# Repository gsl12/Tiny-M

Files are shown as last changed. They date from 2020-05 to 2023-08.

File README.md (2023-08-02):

# Tiny-M   
   
### !!!!!!!!!!!!!! August 2023 !!!!!!!!!!!!!!   
Due to a serious illness, I cannot continues the project.   
Unfortunately i cannot tell, when i could work again.   

[V5 beta](https://github.com/gsl12/Tiny-M-V5-beta)

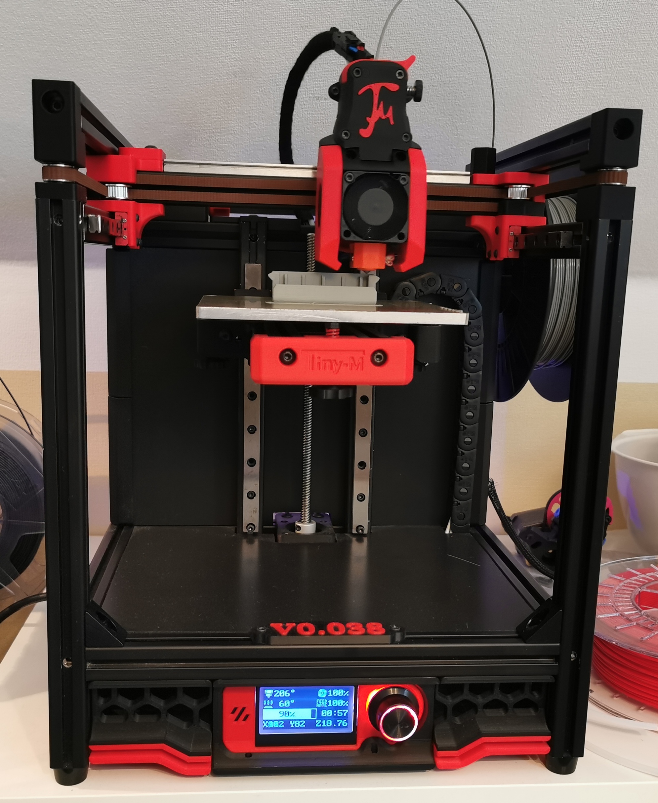
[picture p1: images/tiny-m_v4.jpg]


A compact printer with build volume: 150x150x150 mm

This is a Corona project.  
It is based on [Voron V0](https://github.com/VoronDesign/Voron-0) .  

Bowden and direct drive extruder using [CroXY's Sailfin](https://github.com/CroXY3D/Sailfin-Extruder), [Annex Engineering's Sherpa Mini](https://github.com/Annex-Engineering/Sherpa_Mini-Extruder) or [Bondtech's LGX Lite](https://www.bondtech.se/product/lgx-lite-extruder-custom/) are now available.  

### Current Version is V4:  

Latest source whole printer:  [Tiny-M V4 Onshape](https://cad.onshape.com/documents/f842588d372acab22a4ce687/w/3332acdd7c7bf7fc53ddefb6/e/ce1bfb58b96a9bb3b38b0502)

Old source is available at [Tiny-M V3 Onshape](https://cad.onshape.com/documents/d2a24a4147c3d522115f6ea5/w/d8f44be5c0a081fbf527e154/e/debb6c2779e27f86389232d5).

This is my first project of this kind. Maybe something will be missing, is not well documented, or just messy. I apologize for that.  Join the [Discord](https://discord.gg/tmZkjWs) to meet other Tiny-M builders and have your questions answered.

## Why the whole thing?

I had many 3D printer parts in my pocket from my old no longer used printer. 
I cleared out my pocket and took what I had in the box without buying anything new.
After checking all parts, I recognize, that I could build a converted Voron V0 with this parts.

### Hardware

    - 2020 Nut 5 I-Typ alu profiles (6mm wide slot Misumi 2020 will work).  Must have 4.0-4.2mm hole at ends.  B-Typ can work with Helicoils to give a 5mm tapped end.
    - Nema 17 stepper motors
    - 1x 200mm MGN12H for X
    - 2x 200mm MGN9H for Y
    - 2x 200mm MGN12H for Z
    - FYSETC Cheetah V1.1b (TMC2209) or SKR Mini E3 with TMC2209
    - 24V everywhere

### BOM
DRAFT BOM is available now. Thanks to CookieSN!  An updated BOM for V4 is currently in review.

WARNING ! The store Funssor on aliexpress sell a V0 kit with pictures of my Tiny-M. He use picture from github. To be clear IT IS NOT a Tiny-M Kit. Please don't buy it if you want to build a Tiny-M.

### Build Tips
There are 3 versions of the XY-Joins.  V4 is recommended.

- V2 - use 2GT 20T pulleys - No Set Screw Hub
    - The outer diameter of the flanges from the pulleys for XY Joins will not fit.
    - You will need to grind the flanges to fit.
- V3 - use 2GT 20T toothed idler and no M5 Nuts
- V4 - split into 3 parts
    - removed one M5 screw for better alignment
    - optimized belt path to use E3D idler (10mm high) or chinese (9mm high)
    - some design changes
    - more rigid

Parts are best printed out of ABS or ABS+ with 0.4 nozzle with 0.48 extrusion width, 0.2-0.3 layer height, 5 top/bottom layers, 4 perimeters, 40% infill (triangular recommended).  Skirts can be printed out of pretty much any filament type.

There are drill and tapping jigs if you wish to drill and tap your extrusions yourself.  The drilled holes are for blind joints and aren't necessary if using corner brackets.

[Mark Hoy's Excellent Build Log](https://github.com/mark-hoy/tiny-m-build)

[Aku's Build Pix](https://photos.google.com/share/AF1QipNcXcmM3RKy_vv-VFk4SFu25SVPCTLMsn6qd6mMj0eABvdKW5LyGL7gtdgspUF8wQ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)

### User Mods
There are several user mod STLs in the [usermods](https://github.com/gsl12/Tiny-M/tree/master/usermods) directory.

#### V4 Mods
[Belted Z Mod](https://github.com/gsl12/Tiny-M/tree/master/usermods/belted_z_mod)

[190^3 Mod which uses Prusa mini bed plates](https://github.com/gsl12/Tiny-M/tree/master/usermods/190mm_prusa_mini_mod)

[All Metal Bed Undercarriage](https://github.com/gsl12/Tiny-M/tree/master/usermods/all_metal_bed_undercarriage)

[5mm Shoulder Screw Mod, (also works with B-Typ extrusions)](https://github.com/gsl12/Tiny-M/tree/master/usermods/shoulder_screw_mod)

[5mm Dowel Pin Mod](https://github.com/gsl12/Tiny-M/tree/master/usermods/5mm_idler_pins)

[Rear Cable Guide](https://github.com/gsl12/Tiny-M/tree/master/usermods/rear_cable_guide)

[Tophat Mod](https://www.prusaprinters.org/prints/64115-tiny-m-voron0-mod-tophead) - Note, an official tophat is in development.

#### V3 Mods
[Xile's Sherpa Direct Drive Toolhead](https://github.com/Annex-Engineering/Sherpa_Mini-Extruder/tree/master/Toolheads/Xile_Tiny_M)

[Ocho Camino's Sailfin Direct Drive Toolhead](https://github.com/CroXY3D/Sailfin-Extruder)

### Discord

The [CroXY Discord](https://discord.gg/tmZkjWs) has a tiny-m channel where several Tiny-M builders hang out.  Be sure to check the #tiny-m-faq channel

# Images

V3  

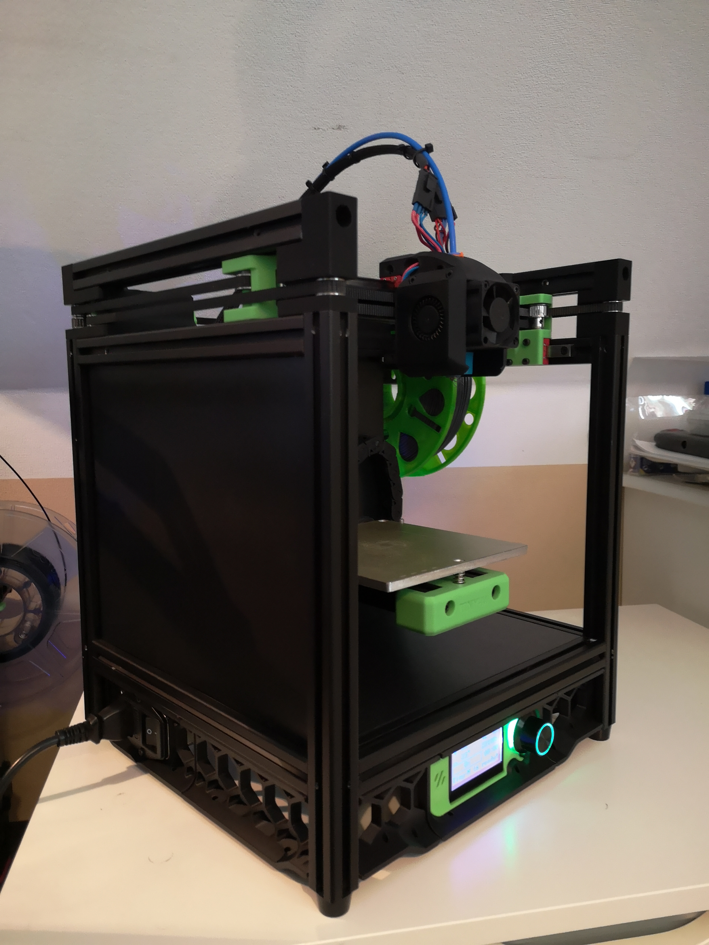
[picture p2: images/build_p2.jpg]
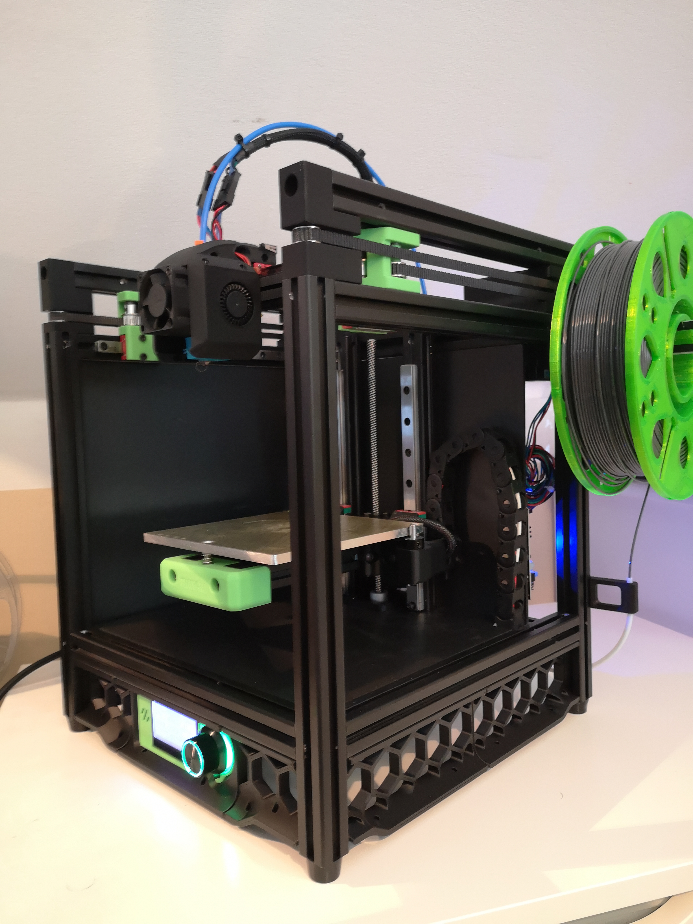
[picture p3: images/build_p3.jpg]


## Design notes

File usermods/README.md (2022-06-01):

### User mods

* tiny-m_tap_guide.stl : guide for tapping ends of 2020 extrusions (danielfmo)
* tiny-m_drill_guide.stl: drill guide for blind joint acccess holes (danielfmo)
* ab_drive_top_raised.STL : On some steppers the screws bottom out.  This thickens the plastic. (Xile)
* Knob_Wrench.stl : Tool to turn the tensioning knobs (Xile)
* Panel_Holder_1.STL : Panel holders keep panels from sagging - (Xile, modified from design by Anlin at Annex Engineering)
* PanelClip_v2_1.stl : Hold exterior panels on - (Xile, Modified from design by Anlin at Annnex Engineering)
* front_bed_mount_proud_text.stl : (Ocho Camino) Front of bed with text raised so you can do a filament swap.
* LRS-150_Mount.STL : Mount for Meanwell power supply (Xile)
* SKR_Mini_Mount.STL : Mount for SKR Mini (Xile)
* Raspi_Mount.STL : Mount for Raspberry Pi (Xile)
* Buck_Converter_Mount.STL : Mount for [Buck converter](https://smile.amazon.com/gp/product/B07N3QT628/ref=ppx_yo_dt_b_search_asin_title?ie=UTF8&psc=1]) for Raspberry Pi 5V (Xile) 
* Cover_No_Logo.STL : No logo version of screen cover
* door_handle: A handle for the enclosure door

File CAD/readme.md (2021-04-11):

# Current Version is V4:  

latest source whole printer:  [Tiny-M V4 Onshape](https://cad.onshape.com/documents/1523b676d2485ac19dbd60ec/w/d40ca3d72ed1f4079efb6497/e/a8deb399653e35f8f0a5baa5)

V4 folder includes separated CAD files for each V4 part.

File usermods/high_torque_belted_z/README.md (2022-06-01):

### High Torque Belted Z

- @AgentL3r#0333

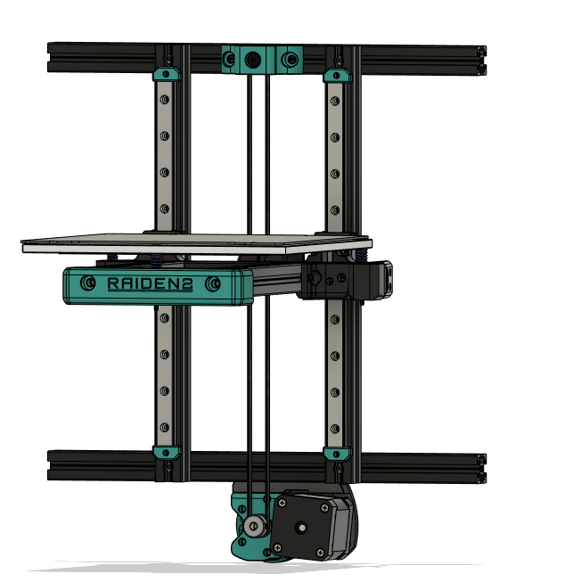
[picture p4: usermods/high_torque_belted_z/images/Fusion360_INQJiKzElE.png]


## Features and Rationale
- Allows for any size of NEMA17 motor to be used, increasing versatility and mitigates the need for slimline/pancake motors 
- Motors with higher detent torques can be used to prevent bed drop on power loss (after 4:1 gearing)
- Gearbox is mounted under the electronics enclosure leading to more space for electronics mounting
- Compatible with both 190mm³ and 150mm³ builds **MUST USE MODIFIED PARTS BY nehiLo#1732**
- Shoulder screw compatible upper z idler
- Arguably less Z artifacting due to no leadscrew
  
## Bill of Materials

Fasteners
- M3x5x4 mm threaded insert x5
- M3 washer (1mm) x3
- M3 shim (0.5mm) x3
- M3x6 BHCS x4
- M3x10 SHCS x4
- M3x20 SHCS x6
- M5 t-nut x7
- M5x10 BHCS x4
- M5x20 BHCS x2
- M5x28 BHCS OR M5x16 SHOULDER SCREW with 5mm shoulder x1
- M5x60 dowel pin

Motion
- F695-2RS bearing x2
- 20T 2GT pulley x2
- 80T 2GT pulley x1 (CAN ALSO USE PRINTED VORON M4 80T)
- 188mm 2GT 6mm belt loop
- some 2GT 6mm belt
- 20T 5mm bore idler

Electronics
- NEMA17 motor

## Assembly
It is best to refer to the CAD  model for guidance on how to build this system.

**Gearbox:**
Insert the four heatset inserts into the back of the shaft guide and press-fit the F695-2RS bearing as follows:
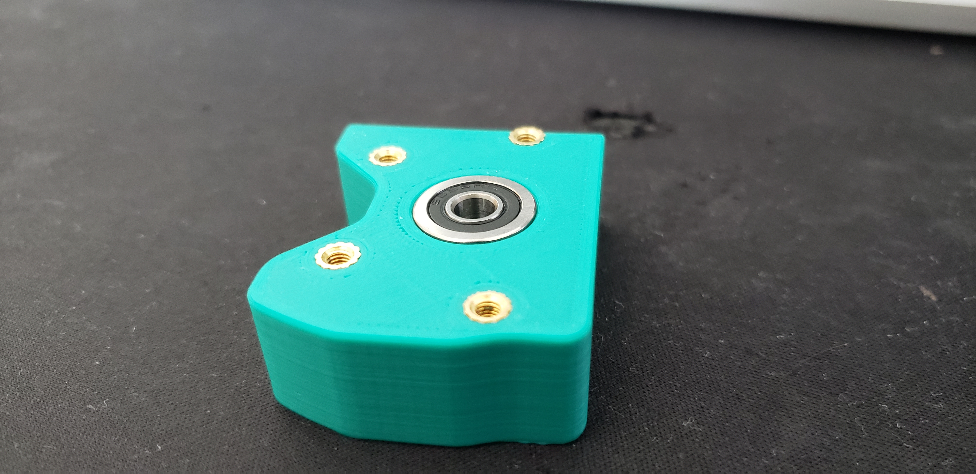
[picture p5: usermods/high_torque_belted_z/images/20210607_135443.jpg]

Press fit an F695-2RS bearing onto the motor plate.

Attach the motor plate to the bottom of the 2020 extrusion on your printer using two M5x10mm screws and two M5 t-nuts. Ensure you use the flat edge and a pair of calipers to correctly position the motor plate so that the pin is centered.

Attach the shaft guide using four M3x20 screws.

Insert the 5x60mm shaft through the motor plate and shaft guide, ensuring it spins freely in the bearings.

The pulleys can now be attached:

80T pulley --> printed spacer --> F695-2RS --> F695-2RS  --> 0.5mm shim --> 20T pulley

Tighten all grub screws.

Insert the remaining 20T pulley onto the shaft of the NEMA17 motor. Screw the motor to the motor plate using M3x10 screws (not fully tight as you'll need the motor to swivel for tension) and an M3 washer. During this, ensure the belt loop wraps around the 20T and 80T pulley. You can now tension the pulley and fully tighten all motor mounting screws. The gearbox is now complete.

**Idler:**
The upper idler is simple to assemble with a 20T idler sandwiched between two 0.5mm shims. Attach this to the top 2020 extrusion as per the CAD model.

**Tensioner:**
Insert the final heatset insert into the hole at the TOP of the tensioner.

Attach the tensioner to the back of the Z carriage using the M5x20mm screws and two M5 t-nuts. Positioning at this point isn't important.

Insert the two M3x20 screws into the tensioner. At this point, you can route the belt. 

The belt will wrap around the M3x20 screws so that the teeth indexes with itself, creating a very secure hold. Place the printed block in the center of the tensioner with the hole facing up.

Using the M3x6mm screws, secure the backplate.

Finally, use an M3x10 screw to tension the belt by pressing the printed block.

This assembly is fiddly and takes a while to get assembled - especially the belt tension. The system works very well and has given me excellent results.

Double check your spacing for everything prior to turning on the system - refer to the CAD if in doubt.

For any questions, feel free to get in touch with me on the TinyM Discord.

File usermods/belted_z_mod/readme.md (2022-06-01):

### Belted Z Mod for 150mm and 190mm Tiny-M

@quasi

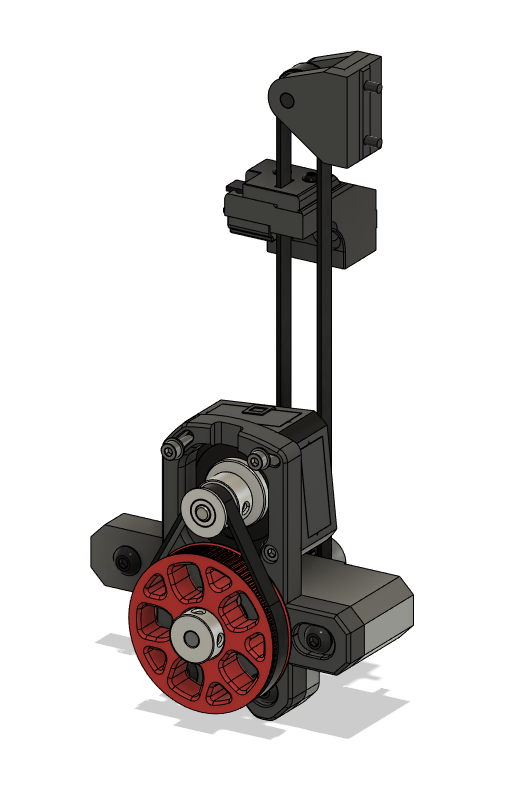
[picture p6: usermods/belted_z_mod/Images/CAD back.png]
Back


Modified from V0 belted z mod for Tiny-M printer, 2020 extrusions, and to upgrade some bolts from M3 to M5.

CAD shows a printed 80T gear because I copied that over from the V0 belted z files, but I used a metal 80T gear.

The M5x20mm screws need to be BHCS for clearance with 80T gear, but all other bolts can be either SHCS or BHCS.

Print the Bottom Frame Bracket 190.stl version if using this on a 190mm^3 Tiny-M

[sample printer.cfg changes](https://github.com/gsl12/Tiny-M/blob/master/usermods/belted_z_mod/beltedzstepper.cfg.txt)

#### BOM (US Sources)
##### Electronics	
- LDO NEMA17 42STH20-1004ASH	[PrintedSolid](https://www.printedsolid.com/collections/motors/products/ldo-nema-17-high-temp-voron-ldo-42sth20-1004ashvrn)  other 20 or a 25mm stepper 0.9 or 1.8 deg should work
##### Motion	
- F695-2RS Bearing [Amazon](https://www.amazon.com/F695-2RS-Bearing-5x13x4mm-Miniature-Bearings/dp/B07VMJLXLH)
- 1x 5mm shaft	78 mm	- I recommend measuring for yourself	[Amazon](https://www.amazon.com/Sydien-100mm-Solid-Stainless-Airplane/dp/B083LDBTLD)
- 1x 2GT Belt Loop (6mm wide) 188mm			[AliExpress](https://www.aliexpress.com/item/4000397043382.html)
- 1x 2GT Open Belt LL-2GT-6 (6mm wide) 10M			[AliExpress](https://www.aliexpress.com/item/32853559638.html)
- 1x 2GT 20T Pulley 6mm, 5mm Bore			[AliExpress](https://www.aliexpress.com/item/32995102911.html)
- 1x 2GT 16T Pulley 6mm, 5mm bore			[Amazon](https://www.amazon.com/gp/product/B01IMPM44O)
- 1x 2GT 80T Pulley 6mm, 5mm Bore			[AliExpress](https://www.aliexpress.com/item/32782605159.html)
- 1x 2GT 20T Toothed Idler 6mm, 5mm Bore		Alternate to 2 F695-2RS bearings	[AliExpress](https://www.aliexpress.com/item/32726309946.html) or better quality: [AliExpress](https://www.aliexpress.com/item/33023133633.html)
#### Hardware	
- Xx 5x10x0.5 Shim Ring			[AliExpress](https://www.aliexpress.com/item/32917948919.html) Qty as necessary.  
- 1x M3x5x4 Heatset Inserts		[AliExpress](https://www.aliexpress.com/item/4000232858343.html?spm=a2g0s.9042311.0.0.21164c4dGhWHhY)
- 2x M3 roll in T-nuts		[AliExpress](https://www.aliexpress.com/item/32805163712.html)
- 4x M5 roll in T-nuts			[AliExpress](https://www.aliexpress.com/item/32805163712.html)
- 2x M3 washer			
- 1x M5x40 SHCS			
- 3x M5x20 BHCS		These NEED to be BHCS for clearance with the 80T gear, all others can be SHCS or BHCS interchangeably	
- 1x M5x16 BHCS			
- 3x M3x12 SHCS			
- 1x M3x20 SHCS

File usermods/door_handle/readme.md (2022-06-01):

The original model provided no handle for the door, so i made one. It is derivatived from the Voron 0.1 door handle. I also added fitting corner pieces.

BOM:
- 2\* M3\*10 screws
- 2\* M3 t-nuts or hammer nuts
- VHB tape
- 8\* 6 mm x 3 mm magnets  

DSCF0841

DSCF0839

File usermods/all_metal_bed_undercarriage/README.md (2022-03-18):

### All Metal Bed Undercarriage

- @Ocho Camino

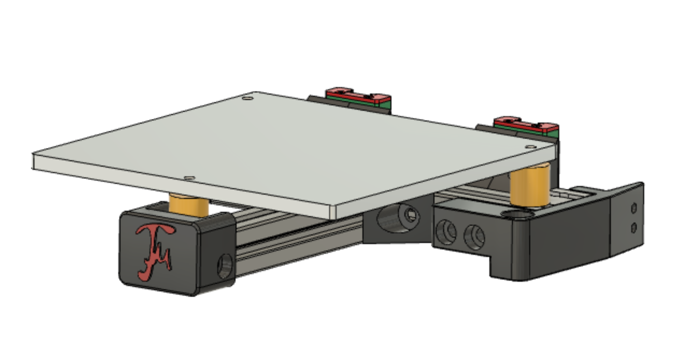
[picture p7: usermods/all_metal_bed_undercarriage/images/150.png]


## Rationale
The existing bed mounts are made of ABS and flex somewhat.   Making the entire bed undercarriage out of metal greatly reduces this flex.

## Status

  Alpha.  Still testing.  There could be some changes.
  
## BOM

150mm Bed:
- 1x HFSB5-2020-160-AH80-AV10-BV150
- 1x HFSB5-2020-160 (with 4 3mm clearance holes drilled for the MGN12 mount screws. Use MGN12_drill_jig.stl)
- 1x HFSB5-2020-133-RTP-AV10 (Misumi). 

190mm Bed:
- 1x HFSB5-2020-200-AH100-AV10-BV190 
- 1x HSFB5-2020-200 (with 4 3mm clearance holes drilled for the MGN12 mount screws.  Use MGN12_drill_jig.stl)
- 1x HFSB5-2020-173-RTP-AV10

Common:
- 6x Openbuilds Angle Brackets [Openbuilds](https://openbuildspartstore.com/black-angle-corner-connector/) [Ali Express](https://www.aliexpress.com/item/32899575950.html)
- 3x 16mm long silicone bed mounts [Amazon](https://smile.amazon.com/dp/B07RZKF8MB?psc=1&ref=ppx_yo2_dt_b_product_details)
- 3x Bed Adjusters (reuse existing) [Ali Experss Style B or D](https://www.aliexpress.com/item/4000421280308.html)
- 3x 45mm (or 50mm) FHCS screws.  45s protrude only 2.3 mm below the extrusion, so 50 is probably better.
- 4x M3 washers (at least 6mm OD) - [ALT Ali Bling](https://www.aliexpress.com/item/32968161596.html)
- 4x M3x8 SHCS (might need M3x10 with the Alt Ali Bling)
- 11x M5x6 BHCS
- 1x M5x12 SHCS
- 1x M5x16 SHCS

## Assembly

Print the parts (ok, it's not all metal, but the load bearing parts are). The nosepiece can be printed with a filament swap for a contrasting color for the logo.  

Note the rear two holes on the bed are in slightly different positions than on stock Tiny-M.  They are 12mm from the rear.
Use the template (TBD) to drill the two countersunk M3 holes.   

The underbed assembly is made of 3 pieces of 2020.  The rear piece attaches to the MGN12 cars.  The middle piece sisters to the rear piece and also supports the bed at each end in the rear.  The front piece is the forward pointing spar that supports the bed at the middle in the front.

The rear 2020 piece will need to be drilled with 4 3mm clearance holes to attach it to the MGN12 car.  Use the MGN12_drill_jig.stl to drill these holes, from each side of the 2020.

If you ordered the other 2020 parts without Misumi drilling for you, you will need to use the drill guide. The middle 2020 that is is sistered to the rear 2020 piece needs a 3mm vertical clearance hole 10mm from each end, and a 5mm horizontal clearance hole 30mm from each end (middle_front_drill_jig.stl).   Additionally that piece needs a 5mm horiztonal clearance hole centered on the extrusion - use middle_jig.stl centered on the extrusion.

The front piece is tapped M5 at the rear and has a 3mm clearance hole drilled vertically 10mm from the front of it (middle_front_drill_jig.stl).

Assemble the middle and front spar 2020 pieces to form a tee.   The two angle brackets that support the forward spar can be any type of angle bracket. Make sure this connection is solid and doesn't twist or flex.   Attach the spar to the tapped hole with a M3x8 BHCS for more rigidity. 

The Openbuilds corner brackts screw into the top screw holes of the MGN12H cars. Attach them to the rear 2020 piece.  The rear 2020 is attached to the lower screw holes of the MGN12H car via M3x16 SHCS.

Attach the tee piece to the rear piece with 2 M5x6 BHCS

The rest of the parts assembly should be straightforward.

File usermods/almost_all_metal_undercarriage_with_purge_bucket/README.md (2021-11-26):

# Almost All Metal Bed Undercarriage with Purge Bucket

- @DanielO

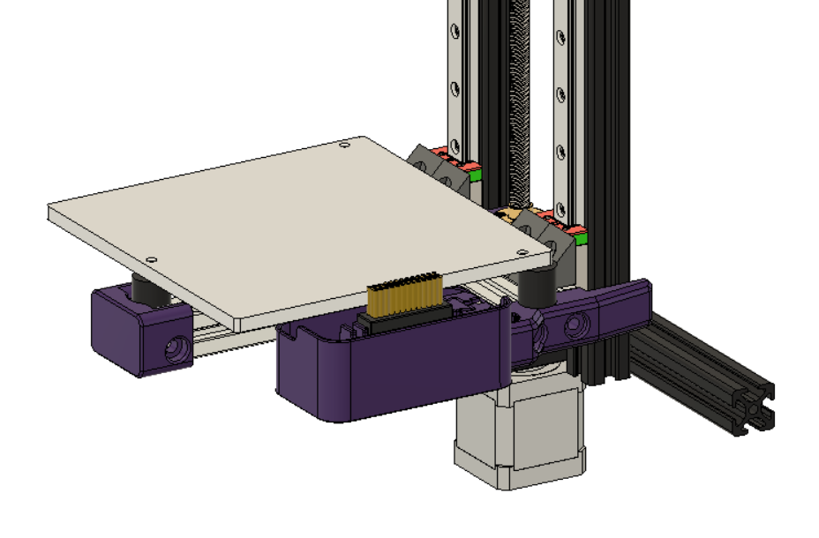
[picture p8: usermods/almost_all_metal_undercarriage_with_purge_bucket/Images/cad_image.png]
CAD

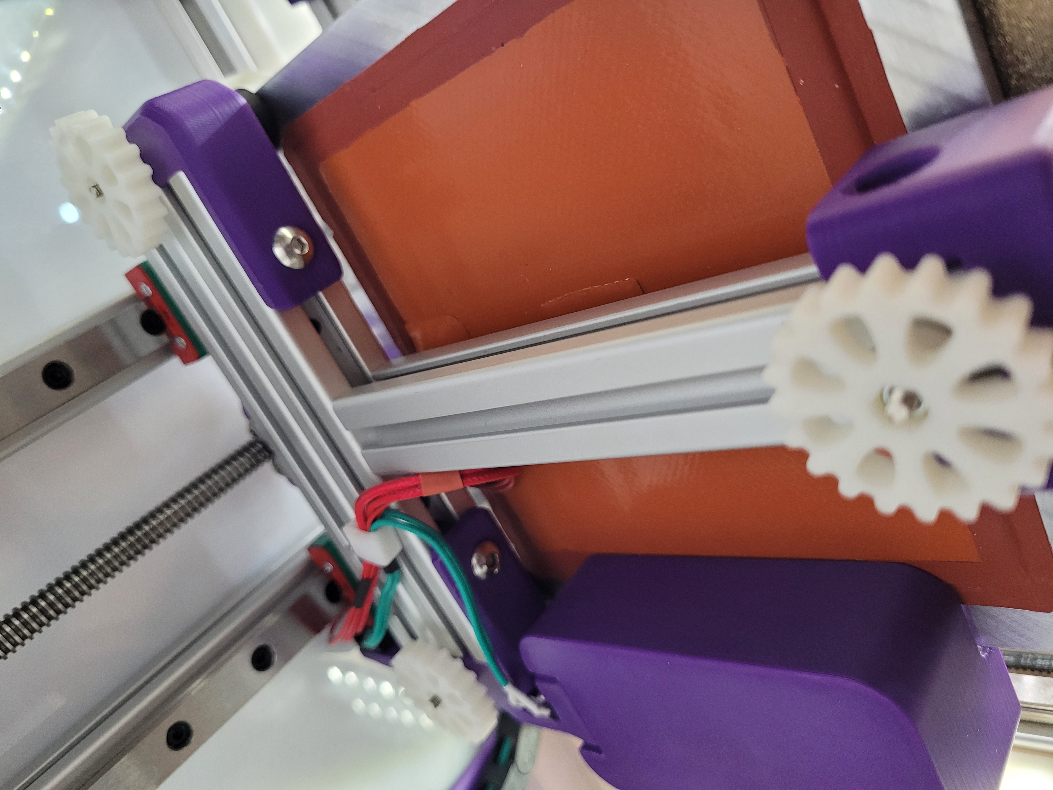
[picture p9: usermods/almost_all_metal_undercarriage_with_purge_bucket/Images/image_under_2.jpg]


## Rationale

The goal was to to create a all meter undercarriage mount inspired in the one created by @Ocho Camino, but using the default BOM extrusions e.g. 3x 130mm long for the 150mm2 version.

The purge bucket and brush were inspired in the [Annex purge bucket](https://github.com/Annex-Engineering/Other_Printer_Mods/tree/master/All_Printers/Purge_Brush_Bucket).

## Status

Tested and validated in a 150mm bed, though in retrospective some improvements could be made:

- move the z endstop a few milimets up in order to be able to use the default BOM 33mm long shaft.
- dimention the purge bucket for the 150mm bed, the available one might be too long.
- design a mount for a belted z mod

## Print Parts

Just need to print one of each STL/3mf.
And the [brush_holder_x1_rev1.STL](https://github.com/Annex-Engineering/Other_Printer_Mods/blob/master/All_Printers/Purge_Brush_Bucket/STLs/brush_holder_x1_rev1.STL) from Annex github.

## BOM

### 150mm Bed

- 3x 130mm long extrusions, from BOM
- 4x M5x8mm for the lead screw mount
- 2x M5x8mm for the from bed mount
- 4x M5x16mm for the side bed mounts
- 3x M5x30mm for holding the extrusions together
- 4x M3x18mm for holding the extrusions against the carts
- 4x M3x10mm and washers for holding the 90deg corners against the carts
- 4x M5x8mm for holding the 90deg corners against extrusions
- a few other M3x8mm for holding the cable chain and the brush
- 4x 6x3mm magnets for the bucket

### 190mm Bed

- not tested / adapted (but should be the same hardware and STLs as the 150mm)

## Klipper Macros for brush and bucket

Node: could and should be improved using variables

```clojure
[gcode_macro NOZZLE_CLEAN]
gcode:
    SAVE_GCODE_STATE NAME=nozzle_clean_state
    G1 X152 Y58 F3000
    G1 Z0.6     F3000
    ; Purge filament macro
    PURGE_FILAMENT
    G90
    ; clean twice
    G1 X152 Y58 F6000
    G1 Y105
    G1 Y58
    G1 Y105
    G1 Y58
    ; Retract
    ;G10
    ; clean once
    G1 Y105
    G1 Y58
    RESTORE_GCODE_STATE NAME=nozzle_clean_state
```

In START_PRINT macro do something like

```clojure
[gcode_macro START_PRINT]
gcode:
  ;================ SET VARIABLES ====================
  {% set T_BED = params.T_BED|default(60)|float %}
  {% set T_EXTRUDER = params.T_EXTRUDER|default(205)|float %}
  TURN_OFF_HEATERS
  M106 S0
  G21                           ; [mm] mode
  G90                           ; Absolute position mode
  M220 S100                     ; reset speed multiplier
  G92 E0                        ; reset e count
  M83                           ; relative Extruder mode
  ;================ INITIALISATION ====================
  G28                           ;  first homing
  ;================ WARM UP ===========================
  G1 X152 Y58 Z5 F3000          ; move nozzle to brush
  {% if printer.heater_bed.temperature < params.T_BED|float*0.85 %}
      M190 S{params.T_BED|float*0.85}
  {% endif %}
  M140 S{T_BED}
  ;G1 X152 Y105 Z0.4 F3000      ; move to approx starting location
  M104 S{T_EXTRUDER|int - 30}   ; set no-ooze extruder temp
  M109 S{T_EXTRUDER|int - 30}   ; wait no-ooze for extruder temp
  ;----------------------- CLEANING---------------------------------
  NOZZLE_CLEAN                  ; call the macro that will clean the nozzle
  ;----------------------- PRECISE HOME-----------------------------
  G28 Z                         ; home z again with nozzle hot
  G1 X152 Y58 Z0.2 F3000        ; move to approx starting location
  ;----------------------- FINAL TEMPS -----------------------------
  M140 S{T_BED}                 ; set final bed temp
  M190 S{T_BED}                 ; wait for final bed temp
  M104 S{T_EXTRUDER}            ; set final extruder temp
  M109 S{T_EXTRUDER}            ; wait for final extruder temp
  ;-----------------------PRIMING-----------------------------------
  PRIME_LINE
  G10;
  G1 Y58                        ; rub on the brush one more time
  G1 Y105
  G1 Y58                        ; move to approx starting location
  G92 E0;                       ; set extruder to Zero
  G1 E0 F100
```

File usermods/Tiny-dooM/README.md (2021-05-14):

### Tiny-dooM

- @Ocho Camino

An outer enclosure around the Tiny-M printer.  This has only been designed in CAD.  Nothing has been done IRL.

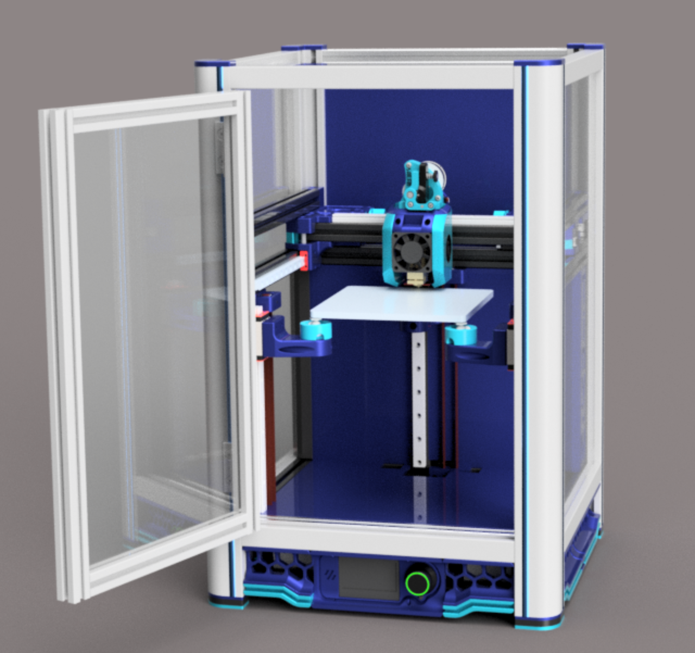
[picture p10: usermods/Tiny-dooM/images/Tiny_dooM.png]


#### BOM

Nothing is changed from the default Tiny-M BOM.  However you will need to drill 2 blind joint access holes in the 4 z corner extrusions.  Those holes should be approx 30mm from the ends and face fore and aft.  They are used to attach the Tiny-M to the dooM frame.

For a 190^3 Tiny-dooM add 50mm to every extrusion length

- 4x HFSR5-404020-500 Corner Posts
- Non-smooth faced extrusion option
  - 8x HFS5-2020-260 Top and bottom horizontals
  - 2x HFS5-2020-217 Front door horizontals
  - 2x HFS5-2020-408 Front door verticals
- Smooth faced extrusion option
  - 2x HFS5-2020-260 Top and bottom rear horizontals (Slots exposed for mounting things)
  - 3x HFSF5-2020-260 - Bottom front, left and right horizontals
  - 3x HFST5-2020-260 - Top front, left and right horizontals
  - 2x HFSF5-2020-217 Front door horizontals
  - 2x HFSF5-2020-408 Front door verticals - you will need to drill holes for hinges and handle
- 2x Hinges [Zyltech](https://www.zyltech.com/aluminum-swing-door-hinge-for-20mm-extrusion-w-mounting-hardware/) alt: HHPNL5-SST hinges
- 24x Internal Corner Brackets [Zyltech](https://www.zyltech.com/t-slot-l-type-90-degree-2020-inside-bracket-12-pack/)
- Door Catch TBD
- Optional: Ninjaflex or similar TPU for feet

Total Hardware Cost for 150 Tiny-dooM (no panels): ~$85

#### Printed Parts

- 4x Top trim pieces
- 4x Feet.  Optionally print black portion using Ninjaflex or similar TPU by filament swap.  Use XX% infill
- TBD Panel retention:  Double pane?  In slot or slight inset from frame?

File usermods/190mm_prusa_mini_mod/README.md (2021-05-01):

### 190^3 Build volume which can use the Prusa Mini Bed Plate.

- @Ocho Camino & @AgentL3r
- Skirts by @AgentL3r

The changes for a 190^3 build volume are fairly simple.   
- All frame extrusions need to be 50mm longer
   * 11x 2020 310mm  (note one more than normal Tiny-M.  This is used as a cross brace about halfway up in the front to stiffen the frame)
   * 4x	2020 350mm
   * 2x	2020 300mm
- All bed extrusions need to be 40 mm longer
   * 3x	2020 170mm
- 1X 250mm MGN12H for X (RobotDigg SUS 440C highly recommended) 
- 2x 250mm MGN9H for Y 
- 2X 250mm MGN12H for Z
- 250mm TR8x4 leadscrew
- Mic6 bed should be 190x190x6mm.  Template for drilling are in the STLs subdir here.
- Bed heater should be 150x150mm.   [Keenovo or AliExpress](https://www.aliexpress.com/item/4000271859036.html?spm=a2g0s.9042311.0.0.27424c4dSLLDSs)
- Three parts need to be 40mm wider.  The front nosepiece and the upper and lower Z supports.  They are in the STLs subdir here
- Skirts are changed.  STLs and CAD by @AgentL3r are here

Note that the nosepiece is modded with proud text, so you can print it text up and do a filament swap for contrasting text.  The holes in the nosepiece have a membrane for printability that must be drilled out 5mm.

If you wish to use blind holes, the extrusion BOM:
- 2x HFSB5-2020-170-TPW		Z carriage.
- 1x HFSB5-2020-170-AH40-BH130	 Z carriage. 
- 2x HFSB5-2020-300-LCV-RCV		Vertical extrusions.
- 1x HFSB5-2020-310	X axis extrusion. 
- 3x HFSB5-2020-310-TPW	Lower front and upper left/right extrusions. 
- 4x HFSB5-2020-310-TPW-AH274		Left and right extrusions. 
- 2x HFSB5-2020-310-TPW-AH93.5-BH216.5	Horizontal Z extrusions.
- 2x HFSB5-2020-350-TPW-RCH-AP60		Front vertical extrusions. 
- 2x HFSB5-2020-350-TPW-RCH-AH60		Rear vertical extrusions.

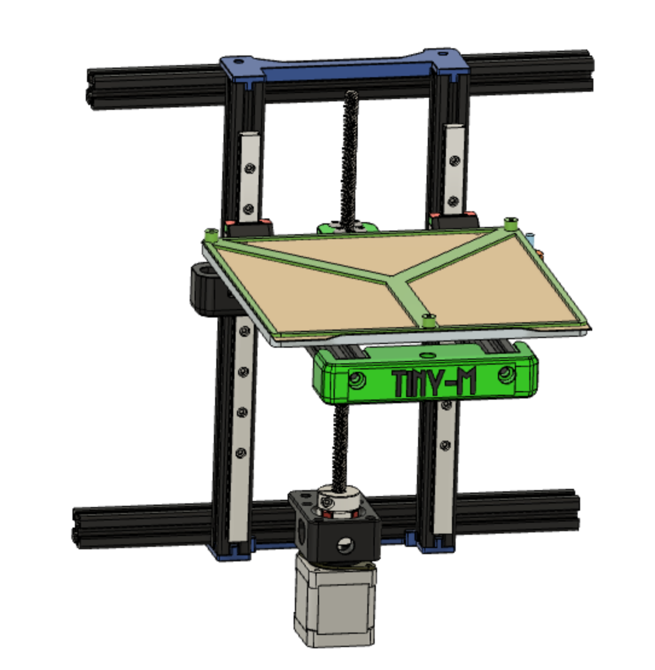
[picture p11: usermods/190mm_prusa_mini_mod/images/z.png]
190^3 Z Assembly


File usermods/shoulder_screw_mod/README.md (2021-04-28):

### Shoulder Screw Mod

by Ocho Camino

This is a mod to use shoulder screws instead of regular metric screws as the shafts for the idlers to ride upon.  

#### Rationale

Shoulder screws are machined to specified dimensions vs screws which are undersized and often have a rough surface.  With undersized screws the contact area of the screw to the inner race of the bearing is much less (ideally a line), creating excessive Hertzian contact stress.  This is hard on the bearing and can create imprecision in the motion of the machine.

#### Description

This mod either uses Misumi 5mm shoulder screws which have M3 threads on the end, or McMaster or other shoulder screws which have M4 threads.  The thread lengths are important on the McMaster M4 version, so if substituting other sources you may need to remove some thread if it's too long and bottoms out.

On the four corners of Tiny-M the ends of the 2020s are tapped M5 for M5 screws.  If using Misumi shoulders, you will need thread adapters.   If using M4 shoulders you will need M4 Helicoils

Print the replacement parts in the STL directory here.

Total cost of this mod is about $25-$30.

#### MISUMI M3 THREADED SHOULDERS
  * 6x 5mmx30 Shoulder Screws M3 Threads, Misumi [SMSB5-30](https://us.misumi-ec.com/vona2/detail/110300249140/?ProductCode=SMSB5-30)
  * 4x 5mmx20 Shoulder Screws M3 Threads, Misumi [SMSB5-20](https://us.misumi-ec.com/vona2/detail/110300249140/?ProductCode=SMSB5-20)
  * 4x M3-M5 308 Type Thread Adapters, AliExpress [M3-M5 308](https://www.aliexpress.com/item/32817733610.html)
  * 2x M3 Tee Nuts

Print the replacement parts, except the M4 versions in the STL directory here.  Install the thread adapters on the 4 M5x30 shoulder screws and secure with Loc-Tite.   These may then be threaded into the tapped M5 hole on the end of the 2020 vertical corner extrusions.  The Tee nuts accept the shoulder screw for the front idler on the AB drives
 
#### FILASTRUDER OR MCMASTER M4 THREADED SHOULDERS
  * 4x 5mmx30 Shoulder Screws, 5-9mm long M4 threads for corners, [Filastruder](https://www.filastruder.com/products/shoulder-screws-bolts?_pos=1&_sid=c5a60b2bd&_ss=r&variant=32520243380295) or [McMaster 92981A055](https://www.mcmaster.com/92981A055/)
  * 2x 5mmx30 Shoulder Screws 5mm long M4 threads for AB drives, [Filastruder](https://www.filastruder.com/products/shoulder-screws-bolts?_pos=1&_sid=c5a60b2bd&_ss=r&variant=32520243380295) or [McMaster 90278A376](https://www.mcmaster.com/90278A376/)
  * 4x 5mmx20 Shoulder Screws, 5-9mm long M4 threads for XY Joins, [Filastruder](https://www.filastruder.com/products/shoulder-screws-bolts?_pos=1&_sid=c5a60b2bd&_ss=r&variant=16712533868615) or [McMaster 92981A042](https://www.mcmaster.com/92981A042/)
  * 1x M4 Helicoil kit, AliExpress [M4x0.7](https://www.aliexpress.com/item/4001157165014.html) or [McMaster 91732A946](https://www.mcmaster.com/91732A946/)
  * 2x M4 Tee Nuts

Print the replacement parts (the M4 versions) in the STL directory here.  Install M4 helicoils in the 4 corner 2020 extrusions.   The Tee nuts accept the shoulder screw for the front idler on the AB drives 

#### EU Folks using 20x20 B-type groove 6 and M4 THREADED SHOULDERS
  * 4x 5mmx30 Shoulder Screws, 8mm long M4 threads for corners, Drasse [460119196](https://www.drabbe.nl/p/iso-7379-5-m4-30/100351/)
  * 2x 5mmx25 Shoulder Screws 8mm long M4 threads for AB drives, Drasse [460119221](https://www.drabbe.nl/p/iso-7379-5-m4-25/100350/)
  * 4x 5mmx20 Shoulder Screws, 8mm long M4 threads for XY Joins Drasse [460119215](https://www.drabbe.nl/p/iso-7379-5-m4-20/100349/)
  * 4x M4-M6 308 Type Thread Adapters, AliExpress [M4-M6 308](https://www.aliexpress.com/item/32817733610.html)
  * 2x M4 Tee Nuts

Print the replacement parts, except the M4 versions in the STL directory here.  Install the thread adapters on the 4 M5x30 shoulder screws and secure with Loc-Tite.   These may then be threaded into the tapped M6 hole on the end of the 2020 B-type groove 6 vertical corner extrusions. The Tee nuts accept the shoulder screw for the front idler on the AB drives

Note, the 5mm shoulders with M4 threads can be sourced from China.  [one possible source - not verified](https://www.aliexpress.com/item/1005001698010943)

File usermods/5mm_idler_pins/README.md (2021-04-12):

### 5mm Dowel Pin Mod
- Ocho Camino

NOTE:  The 5mm shoulder screw mod is recommended over this mod.

This is a mod to use 5mm dowel pins instead of fasteners for the idlers to ride on.  It is based on the V4 gantry.

#### RATIONALE
Dowel pins are exactly 5mm in diameter vs the typical 4.8mm of M5 screws.  This provides a better bearing surface for the inner race of the idler bearings.  Bearing on threads is especially problematic.
It should prolong the life of the bearings and improve print quality because there's signicantly less play.

This mod has not been tested yet!  I am slightly concerned about the rigidity of the front idler mounts as they aren't connected to the corner posts anymore.   

#### BOM
  - 10x 5mmx32mm dowel pins.  [McMaster](https://www.mcmaster.com/91585A569/).  30mm pins may be substituted.  You may also cut down 5mm drill rod or other precision stock to length.  Note some holes can accomodate longer than 32mm pins, so measure and make them longer if need be.

#### INSTALLATION OF PINS
You will probably need to drill out the holes in the parts with a 5mm drill bit.  The idler bearings and toothed idler should slide along the length of the pin.  If the pin is oversized (most dowel pins are), chuck it up in a drill and use 400 grit sandpaper to reduce the diameter.  You shouldn't need to remove more than 0.01mm so check as you go.   

Press the pins into the parts while capturing the bearings/washers/idlers.  If you overcompress the part and bind the bearings, you may need to gently pry the assembly apart a tiny bit.  If the pin is loose, place some thin CA adhesive in the pin holes top and bottom.

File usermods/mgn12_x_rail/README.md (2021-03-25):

Mods to use a MGN12 instead of a MGN9 rail for X.  By FL62michi

NOTE, V4 gantry uses MGN12 rail.

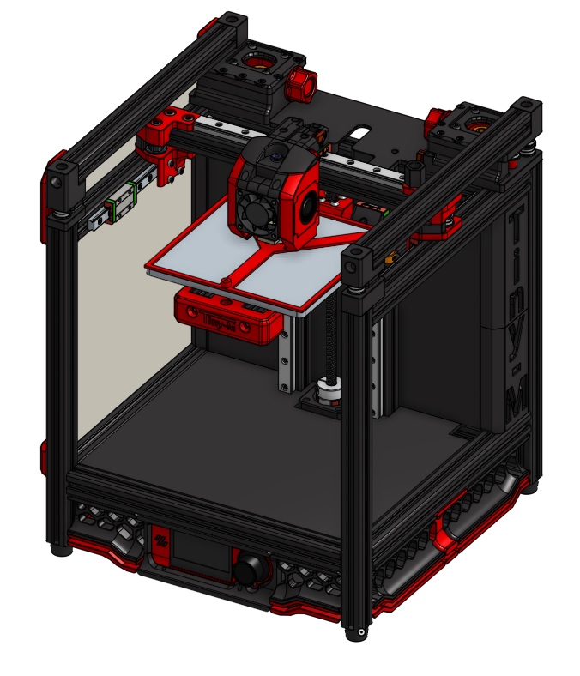
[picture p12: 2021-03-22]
images/CAD_V4.jpg

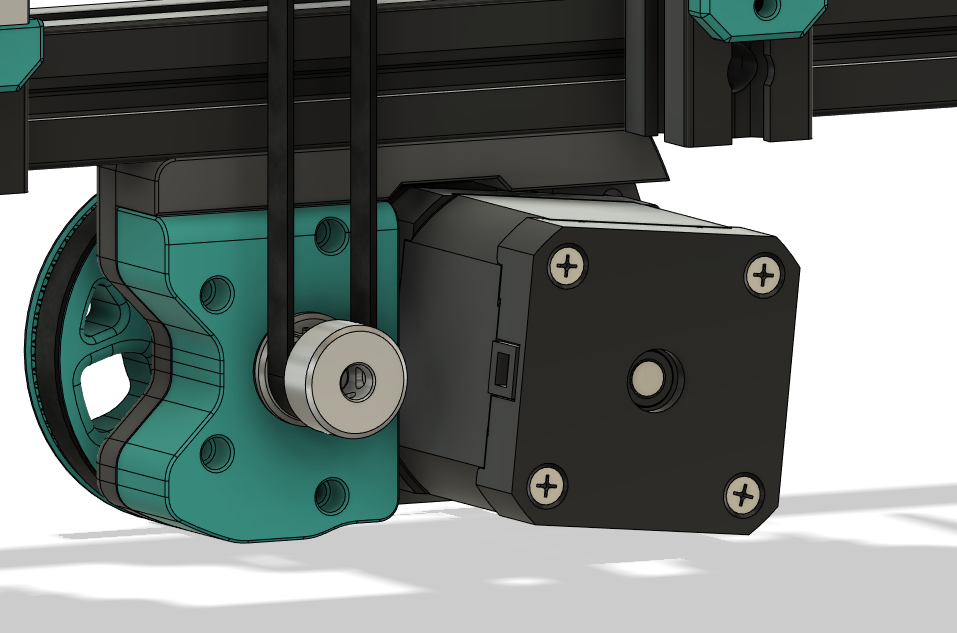
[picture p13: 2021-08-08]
usermods/high_torque_belted_z/images/Fusion360_5fomUjJK1f.png

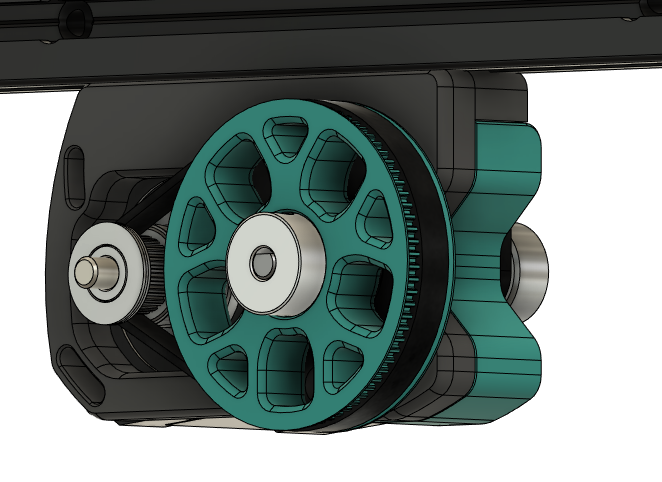
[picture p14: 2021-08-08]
usermods/high_torque_belted_z/images/Fusion360_azjq1ihh6n.png

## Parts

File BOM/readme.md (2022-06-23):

The .XLSX bom here is ancient and deprecated.

[Recommended V4 BOM with US, China and some EU sources](https://docs.google.com/spreadsheets/d/e/2PACX-1vQKTQRPsufotex2pgKZs6gdDjUGlbPzPMrz_vgNp8odzEya9Jntykz1X8XHGsFwYE4CXp_6QBfreYBq/pubhtml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)

[Preliminary (V3?) Google Sheets Version with US Sources](https://docs.google.com/spreadsheets/d/1UV62ADl2gtK5vL0fV1nwevR6O9Ppzs0MBe7jnsI-jo4/edit#gid=1444976440)

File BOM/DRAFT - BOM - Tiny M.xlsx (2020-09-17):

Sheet: BOM_Tiny_M
Category | Component | Standard | Qty | Sourcing DE | AliExpress Source | Alternative Source | Notes
Hardware | 5x10x0.5 Shim Ring | DIN 988 5x10x0.5 Shim Ring | 17
Hardware | 5x10x1 Shim Ring | DIN 988 5x10x1 Shim Ring | 6
Hardware | 5x30mm | shaft 5x30mm | 1
Hardware | M2.5x12 SHCS (for dragon hotend only) | DIN 912 M2.5x12 | 4
Hardware | M2x10 self tapping screw for Plastic |  | 15
Hardware | M3 - T-Nut | M3 - T-Nut | 6
Hardware | M3 Brass Heatstake Inserts | M3x5.0x4.0 | 15
Hardware | M3 Nut | DIN 934 M3 Nut | 14
Hardware | M3x10 SHCS | DIN 912 M3x10 | 2
Hardware | M3x12 SHCS | DIN 912 M3x12 | 2
Hardware | M3x20 SHCS | DIN 912 M3x20 | 2
Hardware | M3x25 SHCS | DIN 912 M3x25 | 2
Hardware | M3x30 SHCS | DIN 912 M3x30 | 8
Hardware | M3x35 SHCS | DIN 912 M3x35 | 8
Hardware | M3x40 SHCS | DIN 912 M3x40 | 12
Hardware | M3x50 SHCS | DIN 912 M3x50 | 4
Hardware | M3x8 SHCS | DIN 912 M3x8 | 99
Hardware | M4x8 SHCS | DIN 912 M4x8 | 4
Hardware | M5 T-Nut | M5 T-Nut | 18
Hardware | M5x10 BHCS | ISO 7380-1 M5x10 | 19
Hardware | M5x15 BHCS | ISO 7380-1 M5x15 | 1
Hardware | M5x16 BHCS | ISO 7380-1 M5x16 | 4
Hardware | M5x20 BHCS | ISO 7380-1 M5x20 | 1
Hardware | M5x30 BHCS | ISO 7380-1 M5x30 | 4
Hardware | M5x35 BHCS | ISO 7380-1 M5x35 | 4
Hardware | M5x40 SHCS | DIN 912 M5x40 | 4
Frame | Frame 2020 Typ I 5mm | 300mm | 4 | MyAluProfil.de (https://www.myaluprofil.de/aluminiumprofil-20x20-nut-5-i-typ-.html)
Frame | Frame 2020 Typ I 5mm | 260mm | 10 | MyAluProfil.de (https://www.myaluprofil.de/aluminiumprofil-20x20-nut-5-i-typ-.html)
Frame | Frame 2020 Typ I 5mm | 250mm | 2 | MyAluProfil.de
Frame | Frame 2020 Typ I 5mm | 130mm | 3 | MyAluProfil.de
Electronic | Nema 17 Motor 17HS19-2004S | 17HS19-2004S | 3
Electronic | Omron Mouse Button - Micro Switch | D2F-5L | 4
Electronic | TL dragon hotend |  | 1
Electronic | V6 Hotend 24V | V6 Hotend | 1
Electronic | 4010 Blower Fan | 40x40x10 Blower Fan v1 | 4
Electronic | 4020 DC Fan 24V | 40x40x20 DC Fan | 2
Electronic | Mean Well LRS-150-24 | LRS-150-24 | 1 |  |  |  | Needed for the main electronis (board, motors, lcd, etc.)
Electronic | Mean Well LRS-350-24V | LRS-350-24V | 1 |  |  |  | Needed if you use a 24V heated bed. If not you must use a 110V/220V heated bed.
Electronic | Raspberry Pi 4 | 2GB or 4GB Version | 1 |  |  |  | If you have a Pi 3 you can use this also
Electronic | DC-DC 5V 3A converter |  | 1
Electronic | SKR E3 Mini | Bigtreetech SKR E3 Mini | 1
Electronic | Fysetc Mini 12864 | LCD Display | 1
Motion | GT2 20T Pulley 6mm, 5mm Bore | Powdge GT2 20T Pulley 6mm, 5mm Bore | 3
Motion | F695-2RS | F695-2RS bearing | 20
Motion | 2GT-20T-idler | 2GT-20T-idler | 2
Motion | MGN9-200mm | MGN9 200mm | 3
Motion | MGN12_200mm | linear rail MGN12 200mm | 2
Motion | TR8x8 Lead Screw Nut | lead screw TR8x8 215mm | 1
Motion | 5x8 flexible spider coupler | Stepper Coupler D25L30 | 1
Motion | Nema 17 Damper |  | 1
Buildplate | MIC6 6mm Plate - 150x150mm |  | 1
Buildplate | Silicone AC 120V/240V Heater 100x100mm 100W |  | 1
Buildplate | PEI + 3M 468P (200MP) |  | 1
Buildplate | yellow die springs 8x4x20mm |  | 3
Buildplate | Spring Steel Flex Buildplate 150x150mm (OPTIONAL)
Extruder | Nema 17 Motor 17HS19-2004S | 17HS08-1004S | 1
Extruder | BMG Kit |  | 1
Extruder | PFTE Tube 1m |  | 2
Mics. | Rubber Feed - 21x12 |  | 4 | Amazon.de (https://www.amazon.de/gp/product/B008LTY1NO/ref=ppx_yo_dt_b_asin_title_o00_s00?ie=UTF8&psc=1)
Mics. | Panels side |  | 2
Mics. | Panel bottom |  | 1
Mics. | panel back |  | 1

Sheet: Screw_Consolidated
Hardware | 5x10x0.5 Shim Ring | DIN 988 5x10x0.5 Shim Ring | 6 | x | Hardware | 5x10x0.5 Shim Ring | DIN 988 5x10x0.5 Shim Ring | 17
hardware | 5x10x0.5 Shim Ring | DIN 988 5x10x0.5 Shim Ring | 11 | x | Hardware | 5x10x1 Shim Ring | DIN 988 5x10x1 Shim Ring | 6
Hardware | 5x10x1 Shim Ring | DIN 988 5x10x1 Shim Ring | 1 | x | Hardware | 5x30mm | shaft 5x30mm | 1
Hardware | 5x10x1 Shim Ring | DIN 988 5x10x1 Shim Ring | 5 | x | Hardware | M2.5x12 SHCS (for dragon hotend only) | DIN 912 M2.5x12 | 4
Hardware | 5x30mm | shaft 5x30mm | 1 | x | Hardware | M2x10 self tapping screw for Plastic |  | 15
Hardware | DIN 912 M3x8 | DIN 912 M3x8 | 16 | x | Hardware | M3 - T-Nut | M3 - T-Nut | 6
Hardware | DIN 912 M3x8 | DIN 912 M3x8 | 72 | x | Hardware | M3 Brass Heatstake Inserts | M3x5.0x4.0 | 15
 | DIN 912 M3x8 | DIN 912 M3x8 | 6 | x | Hardware | M3 Nut | DIN 934 M3 Nut | 14
Hardware | heat insert M3x5.0x4.0 | heat set threaded insert | 4 | x | Hardware | M3x10 SHCS | DIN 912 M3x10 | 2
 | heat insert M3x5.0x4.0 | heat set threaded insert | 6 | x | Hardware | M3x12 SHCS | DIN 912 M3x12 | 2
Hardware | ISO 7380-1 M5x16 | ISO 7380-1 M5x16 | 1 | x | Hardware | M3x20 SHCS | DIN 912 M3x20 | 2
Hardware | ISO 7380-1 M5x16 | ISO 7380-1 M5x16 | 1 | x | Hardware | M3x25 SHCS | DIN 912 M3x25 | 2
Hardware | ISO 7380-1 M5x30 | ISO 7380-1 M5x30 | 4 | x | Hardware | M3x30 SHCS | DIN 912 M3x30 | 8
 | M2.5x12 SHCS (for dragon hotend only) |  | 4 | x | Hardware | M3x35 SHCS | DIN 912 M3x35 | 8
 | M2x10 self tapping screw |  | 2 | x | Hardware | M3x40 SHCS | DIN 912 M3x40 | 12
Hardware | M3 - T-Nut sym | M3 - T-Nut sym | 4 | x | Hardware | M3x50 SHCS | DIN 912 M3x50 | 4
 | M3 Heat Threaded Insert | M3 Threaded Insert | 5 | x | Hardware | M3x8 SHCS | DIN 912 M3x8 | 99
Hardware | M3 Nut | DIN 934 M3 Nut | 2 | x | Hardware | M4x8 SHCS | DIN 912 M4x8 | 4
Hardware | M3 Nut | DIN 934 M3 Nut | 12 | x | Hardware | M5 T-Nut | M5 T-Nut | 18
Hardware | M3-T-Nut | M3-T-Nut | 12 | x | Hardware | M5x10 BHCS | ISO 7380-1 M5x10 | 19
Hardware | M3-T-Nut | M3-T-Nut | 26 | x | Hardware | M5x15 BHCS | ISO 7380-1 M5x15 | 1
 | M3-T-Nut | M3-T-Nut | 4 | x | Hardware | M5x16 BHCS | ISO 7380-1 M5x16 | 4
Hardware | M3x10 | DIN 912 M3x10 | 2 | x | Hardware | M5x20 BHCS | ISO 7380-1 M5x20 | 1
Hardware | M3x12 | DIN 912 M3x12 | 2 | x | Hardware | M5x30 BHCS | ISO 7380-1 M5x30 | 4
Hardware | M3x20 | DIN 912 M3x20 | 2 | x | Hardware | M5x35 BHCS | ISO 7380-1 M5x35 | 4
Hardware | M3x25 | DIN 912 M3x25 | 2 | x | Hardware | M5x40 SHCS | DIN 912 M5x40 | 4
Hardware | M3x30 | DIN 912 M3x30 | 2 | x
Hardware | M3x30 | DIN 912 M3x30 | 4 | x
Hardware | M3x30 | DIN 912 M3x30 | 2 | x
Hardware | M3x35 | DIN 912 M3x35 | 4 | x
Hardware | M3x35 | DIN 912 M3x35 | 4 | x
Hardware | M3x40 | DIN 912 M3x40 | 4 | x
Hardware | M3x40 | DIN 912 M3x40 | 8 | x
Hardware | M3x50 | DIN 912 M3x50 | 4 | x
 | M3x8 |  | 4 | x
Hardware | M3x8 | DIN 912 M3x8 | 1 | x
Hardware | M4x8 | DIN 912 M4x8 | 4 | x
Hardware | M5 T-Nut | M5 T-Nut | 1 | x
Hardware | M5 T-Nut | M5 T-Nut | 9 | x
 | M5 T-Nut | M5 T-Nut | 8 | x
Hardware | M5x10 | ISO 7380-1 M5x10 | 7 | x
 | M5x10 | ISO 7380-1 M5x10 | 12 | x
Hardware | M5x15 | ISO 7380 M5x15 | 1 | x
Hardware | M5x16 | ISO 7380 M5x16 | 2 | x
Hardware | M5x20 | ISO 7380-1 M5x20 | 1 | x
Hardware | M5x35 | ISO 7380-1 V2 M5x35 | 2 | x
Hardware | M5x35 | ISO 7380-1 V2 M5x35 | 2 | x
Hardware | M5x40 | DIN 912 M5x40 | 2 | x
Hardware | M5x40 | DIN 912 M5x40 | 2 | x

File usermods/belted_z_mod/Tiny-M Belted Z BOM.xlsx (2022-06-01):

 | Component | Quantity | Notes | Vendor (US) | Link (US)
Electronics | LDO NEMA17 42STH20-1004ASH | 1 |  | PrintedSolid | https://www.printedsolid.com/collections/motors/products/ldo-nema-17-high-temp-voron-ldo-42sth20-1004ashvrn
Motion | F695-2RS Bearing | 5 |  | Amazon | https://www.amazon.com/F695-2RS-Bearing-5x13x4mm-Miniature-Bearings/dp/B07VMJLXLH
 | 5mm shaft | 78 mm | I recommend measuring for yourself | Amazon | https://www.amazon.com/Sydien-100mm-Solid-Stainless-Airplane/dp/B083LDBTLD?s=hi
 | GT2 Belt Loop (6mm wide) 188mm | 1 |  | AliExpress | https://www.aliexpress.com/item/4000397043382.html
 | GT2 Open Belt LL-2GT-6 (6mm wide) - 10M | 1 |  | AliExpress | https://www.aliexpress.com/item/32853559638.html
 | GT2 20T Pulley 6mm, 5mm Bore | 1 |  | AliExpress | https://www.aliexpress.com/item/32995102911.html
 | GT2 16T Pulley 6mm, 5mm bore | 1 |  | Amazon | https://www.amazon.com/gp/product/B01IMPM44O/ref=ppx_yo_dt_b_asin_title_o05_s00?ie=UTF8&psc=1
 | GT2 80T Pulley 6mm, 5mm Bore | 1 |  | AliExpress | https://www.aliexpress.com/item/32782605159.html
 | GT2 20T Toothed Idler 6mm, 5mm Bore | 1 | Alternate to 2 F695-2RS bearings | AliExpress | https://www.aliexpress.com/item/32726309946.html
Hardware | 5x10x0.5 Shim Ring | Varies |  | AliExpress | https://www.aliexpress.com/item/32917948919.html
 | M3x5x4 Heatset Inserts | 1 |  | AliExpress | https://www.aliexpress.com/item/4000232858343.html?spm=a2g0s.9042311.0.0.21164c4dGhWHhY
 | M3 roll in T-nuts | 2 |  | AliExpress | https://www.aliexpress.com/item/32805163712.html
 | M5 roll in T-nuts | 4 |  | AliExpress | https://www.aliexpress.com/item/32805163712.html
 | M3 washer | 2
 | M5x40 SHCS | 1
 | M5x20 BHCS | 3 | These NEED to be BHCS for clearance with the 80T gear, all others can be SHCS or BHCS interchangeably
 | M5x16 BHCS | 1
 | M3x12 SHCS | 3
 | M3x20 SHCS | 1

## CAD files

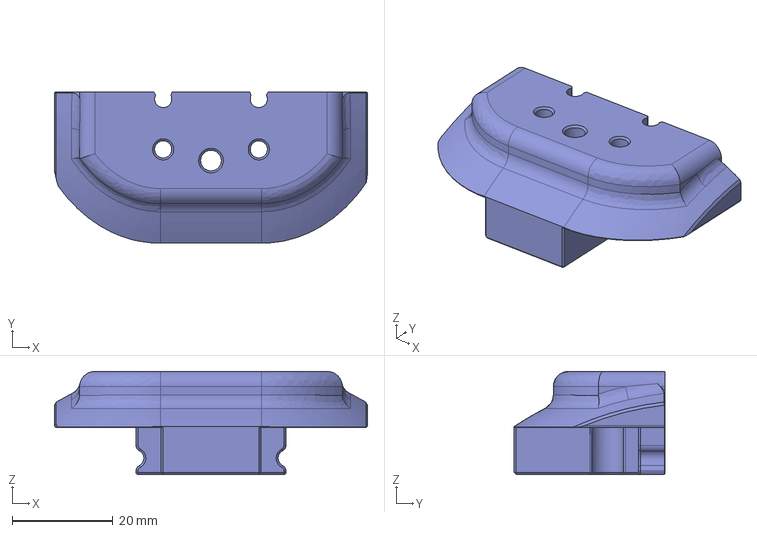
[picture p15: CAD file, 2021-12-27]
CAD/V4/bw_dd_sch_wing_v12_lgx_lite.step
62.2 x 30.0 x 20.5 mm

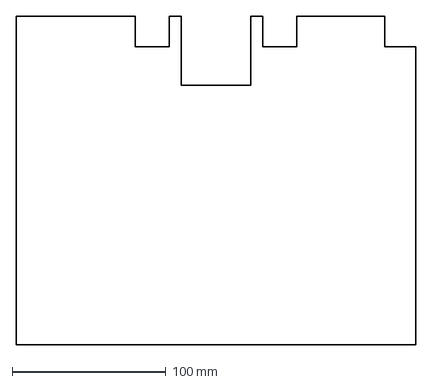
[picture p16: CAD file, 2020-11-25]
DXFs/Deck_Panel.DXF
260.0 x 214.0 mm

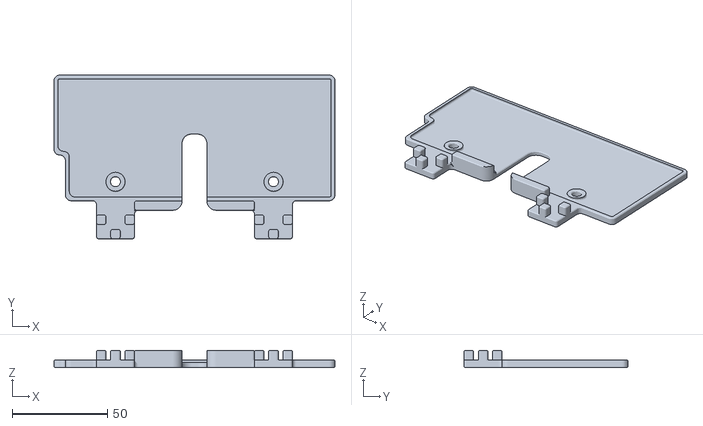
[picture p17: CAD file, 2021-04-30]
STLs/essentials/Bed/z_positioner_upper.stl
147.6 x 86.0 x 9.00

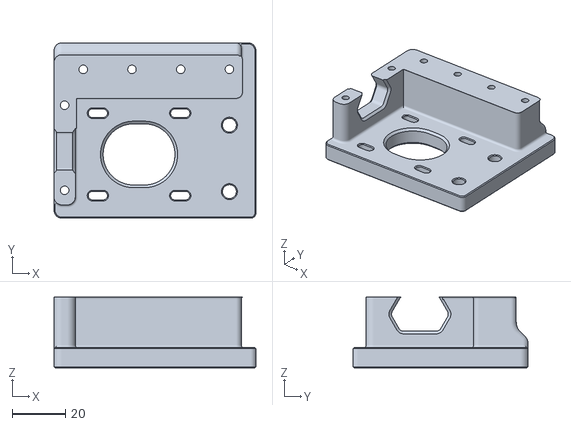
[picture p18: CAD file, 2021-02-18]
STLs/essentials/Gantry/AB_drive_units/ab_drive v4 - a_drive_left_bottom_V4.stl
76.0 x 66.0 x 26.6

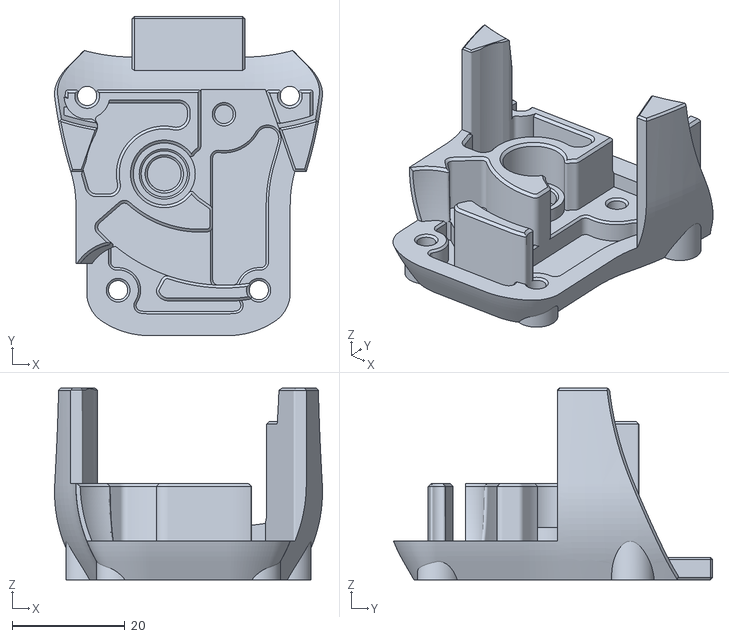
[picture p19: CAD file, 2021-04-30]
STLs/essentials/Gantry/X_Axis/X_Carriage/mini_AB_parts/printed_parts_MGN12_v4 - mini_ab - front_logo.stl
47.6 x 56.7 x 34.0

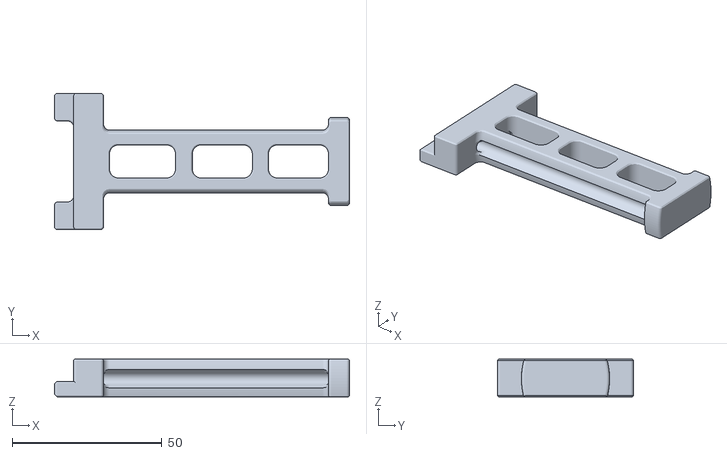
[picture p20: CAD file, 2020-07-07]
STLs/essentials/Spool_Management/printed_parts - Spool Holder-5mm_mod.stl
98.4 x 45.4 x 12.5

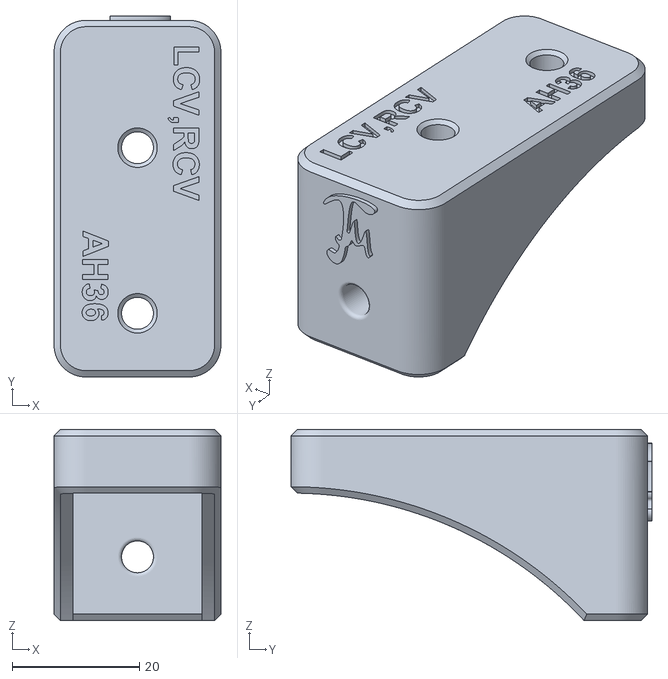
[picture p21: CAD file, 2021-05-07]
STLs/essentials/Tools/Drill_Tap_Jig_B_.stl
26.2 x 56.7 x 30.0

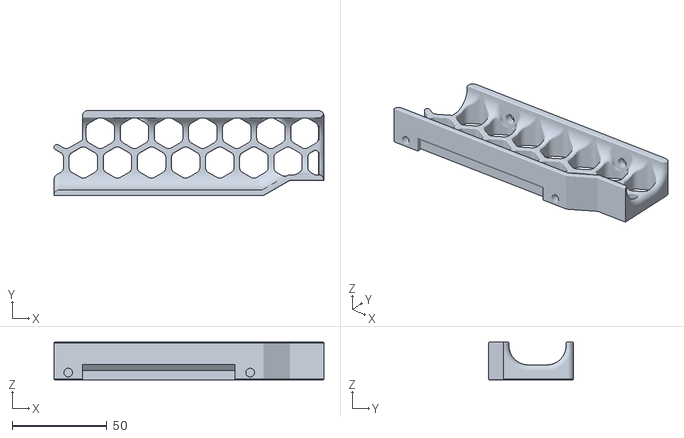
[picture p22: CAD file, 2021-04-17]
usermods/190mm_prusa_mini_mod/STLs/skirt_side_right_x2.stl
142.5 x 44.9 x 20.0

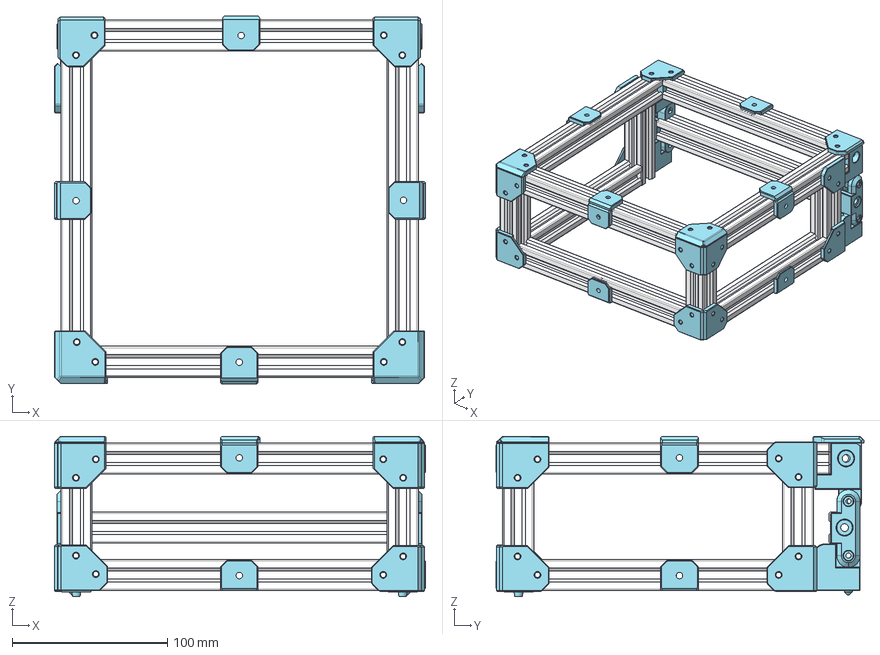
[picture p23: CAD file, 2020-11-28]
usermods/2020_Hinged_TopHat_Print/2020_Hinged_TopHat_CAD.step
238.7 x 236.5 x 103.1 mm

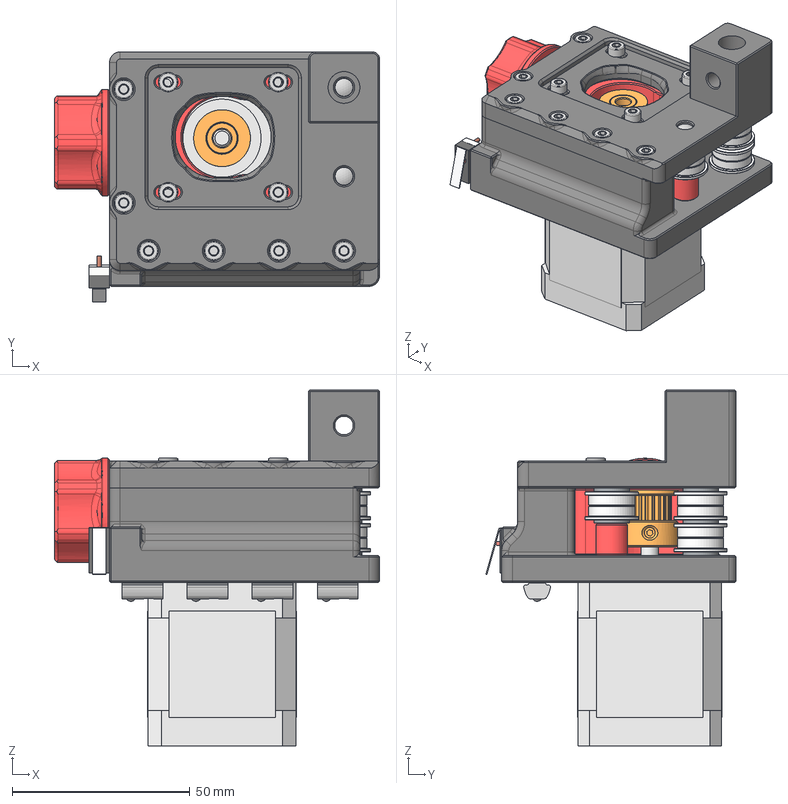
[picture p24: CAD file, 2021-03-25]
usermods/5mm_idler_pins/CAD/ab_drive_unit_right_V4 v4.step
91.5 x 70.4 x 100.2 mm
DIN 912 M3x35 x 8
M3-T-Nut x 4
DIN 912 M3x30 x 2
F695-2RS x 6
DIN 988 5x10x1 Shim Ring x 5
b_drive_right_bottom_V4
DIN 934 M3 x 2
D2F-5L
Motor 17HS19-2004S
GT2_20T
[a]_b_drive_right_tensioner_V4
[a]_b_drive_knop_V4
[a]_ab_drive_spacer_9mm
b_drive_right_top_V4
91595A376_32mm_METRIC ALLOY STEEL DOWEL PIN x 2

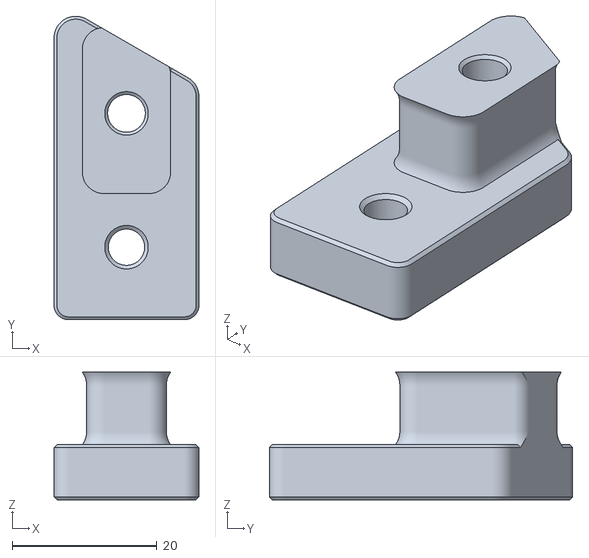
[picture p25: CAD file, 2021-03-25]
usermods/5mm_idler_pins/STL/front_idler_left_bottom_V4.stl
20.0 x 41.8 x 17.6

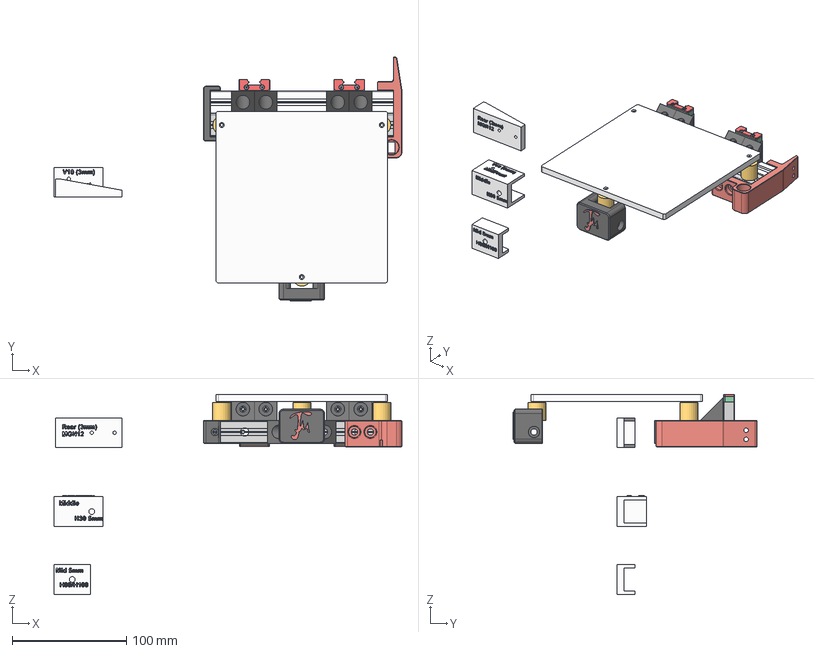
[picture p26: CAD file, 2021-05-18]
usermods/all_metal_bed_undercarriage/CAD/150mm.step
304.4 x 213.7 x 175.0 mm
Bed
MGN12H, LINEAR GUIDE BLOCK x 2
Silicone Bed Spacer
End Cap
Nameplate
HFSB5-2020-160-LCV-RCV-AH30-BH80-CH130
HFSB5-2020-160-Drilled
Z Touch and Chain Mount
Jigs

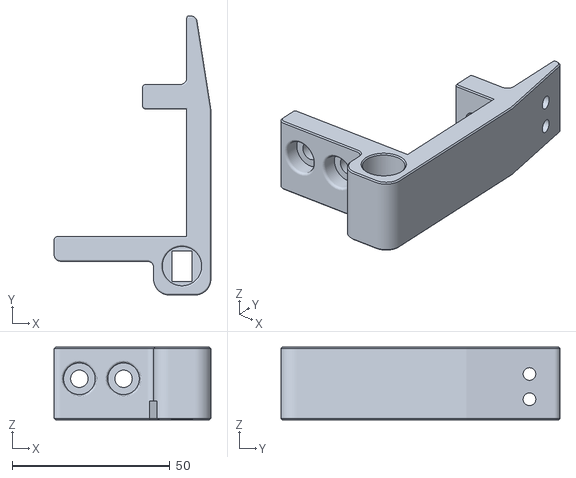
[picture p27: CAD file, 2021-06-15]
usermods/all_metal_bed_undercarriage/STL/Z_Touch_and_Chain_Mount.stl
49.6 x 88.3 x 23.0

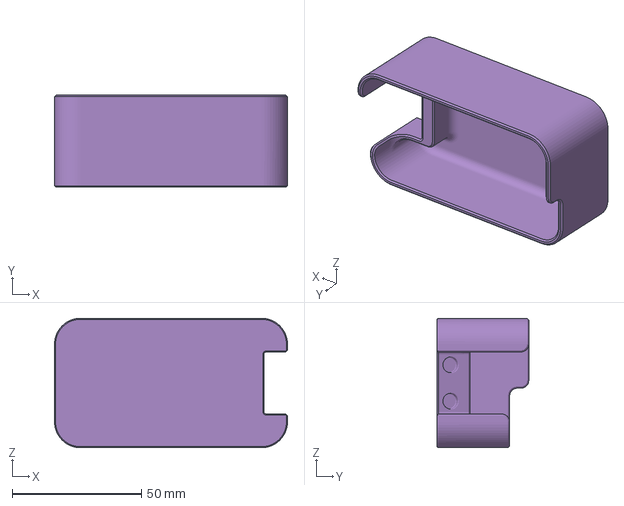
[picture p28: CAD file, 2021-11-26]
usermods/almost_all_metal_undercarriage_with_purge_bucket/STLs/brush_bucket.3mf
90.0 x 35.4 x 50.0 mm

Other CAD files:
STLs/essentials/Gantry/X_Axis/X_Carriage/printed_parts_MGN12_v4 - bw_dd_sch_wing_lgx_lite.stl
usermods/belted_z_mod/STLs/Bottom Frame Bracket.stl
usermods/door_handle/CAD/TinyM Handle v3.step
usermods/door_handle/stl/corner_door_flat(Mirror).stl
CAD/V3/ass_x_carriage_E3DV6.step
CAD/V4/Drill Tap Jigs v4.f3d
CAD/V4/Drill Tap Jigs v4.step
CAD/V4/ab_drive_unit_left_v4.step
CAD/V4/ab_drive_unit_right_V4.step
CAD/V4/enclosure V4.step
CAD/V4/enclosure_V3.step
CAD/V4/front_idler_left_V4.step
CAD/V4/front_idler_right_V4.step
CAD/V4/xy_joint_V4.step
DXFs/Back_Panel.DXF
STLs/essentials/Bed/front_bed_mount_new_logov_4.stl
STLs/essentials/Bed/old/printed_parts - front_bed_mount.stl
STLs/essentials/Bed/printed_parts - front_bed_mount_no_logo.stl
STLs/essentials/Bed/printed_parts - lead screw motor mount.stl
STLs/essentials/Bed/printed_parts - lead_skrew_nut_block_m4 (1).stl
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

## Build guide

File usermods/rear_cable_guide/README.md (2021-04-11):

Trimp pieces and guide for the rear umbilical cable.   By @aku

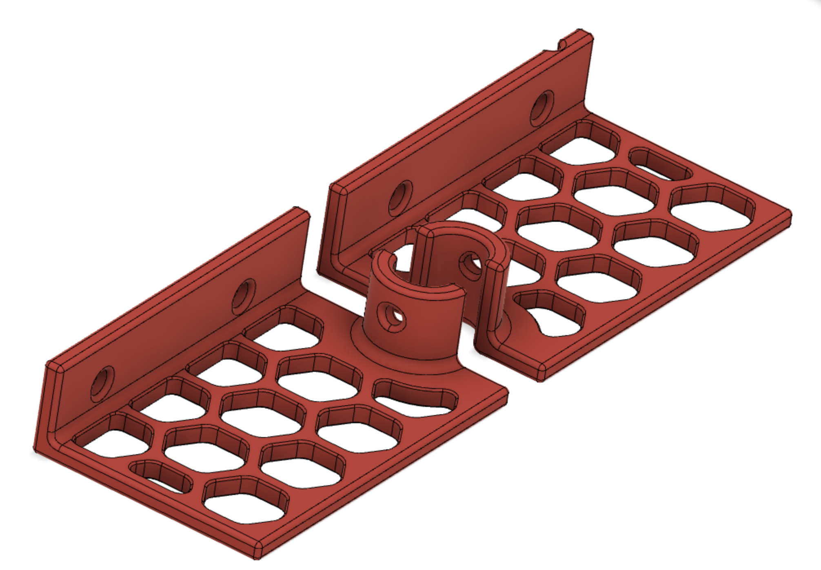
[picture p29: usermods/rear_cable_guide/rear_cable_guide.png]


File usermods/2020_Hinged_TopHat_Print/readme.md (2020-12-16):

DON'T USE THESE YET.  THEY ARE NOT SIZED FOR TINYM.

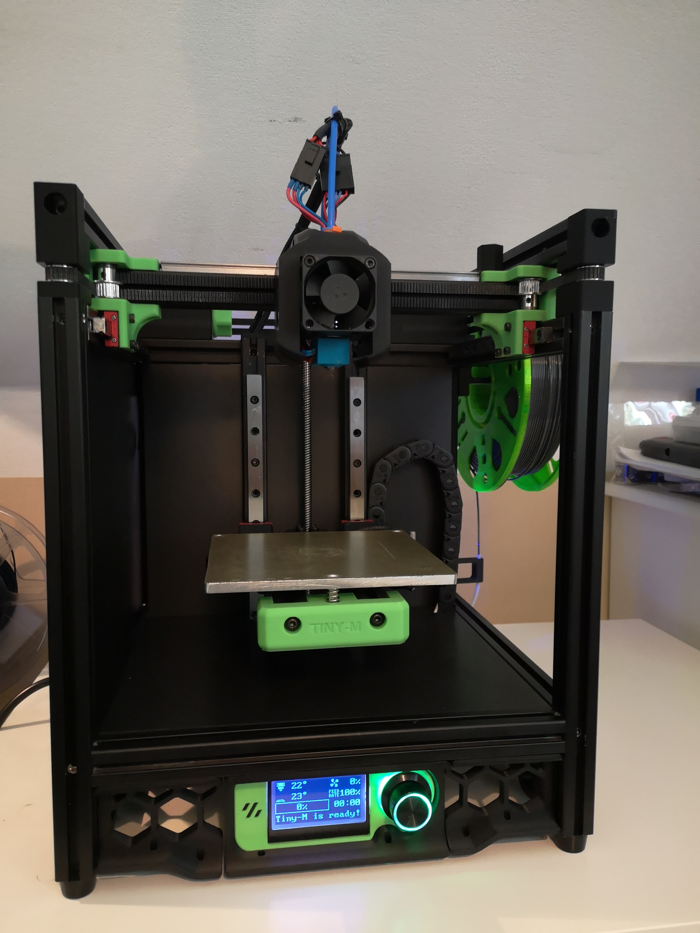
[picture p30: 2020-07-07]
images/build_p1.jpg

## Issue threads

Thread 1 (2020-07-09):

Some Questions

cookieSN, 2020-07-09:
Hi,

before I ask my question, I would like to tell you, that I find your variant of the Voron V0 very cool.

I like the standard voron v0, but the few centimeters more make a huge difference.  Many thanks for your effort.

My question:

Did you only add 30mm to the original for the aluminum extrusion?  (Example: 200mm (voron v0) + 30mm)

Are you thinking to provide a bom (e.g. based on the voron v0 bom)?

Thank you and regards,

CookieSN

gsl12, 2020-07-09:
Hello ,

to your first question.

At the beginning this printer was planned as a small version of a Voron 1.6 with linear rails. So the extrusion lenght was get from the calculator at vorondesign.com for a size of 120x120x130. The goal was not to get a specific build size, but a fixed outside dimension for the frame of 300x300x300mm. Later the V0 was released and i desided to switch to the V0 design. The good point was , that i recognized that with the V0 design a build size o 150x150x150 was possible with extrusions i already had.

to your second question.

I'm working on a BOM at the moment. Onshape has this feature included, some parts are still missing and some parts(like printed part) are not excluded from the BOM in Onshape. Later i will put a excel sheet here.

This is my first project of this kind. Maybe something will be missing, is not well documented, or just messy. I apologize for that.

best regards

GSL12

cookieSN, 2020-07-14:
Hi,

thank you for the quick and comprehensive answer to the questions.

If you need support, just let me know.  Maybe I can help.

I will definitely build your variant of the Voron and look forward to your bom.

Do you use discord?

Best regards from Germany,

cookieSN

gsl12, 2020-07-14:
Yes i use discord. Username same as here.

BTopbas, 2020-09-07:
Thanks for your amazing work! Bom is when will be available?

cookieSN, 2020-09-07:
> Thanks for your amazing work! Bom is when will be available?

Hi, I am working on the BOM. So, maybe end of this week.

hhammarstrand, 2020-09-13:
Another question related to the BOM; can the Tiny-M be built from 2020 V-slot?

cookieSN, 2020-09-16:
Hi guys,

sorry that it took a little longer.

I have attached the BOM to this post, but it is not final yet. The links to the sources (local source, AliExpress, etc.) are still missing. I'll upload an updated version on Sunday. When designing, I stuck to the original BOM from the Voron V0.

If you want any changes, just let me know.
[DRAFT - BOM - Tiny M.xlsx](https://github.com/gsl12/Tiny-M/files/5235476/DRAFT.-.BOM.-.Tiny.M.xlsx)

hhammarstrand, 2020-09-20:
@cookieSN Thank you!

@gsl12 Do you know if it's possible to build the T-M with v-slot extrusions? I have some left from my old printer and it would be nice to be able to use them

gsl12, 2020-09-21:
@hhammarstrand
Because of the MGN9 the Tiny-M has the same restrictions as every other Voron. V-Slot was not recommended while the Nut is to big. MGN9 is 9mm width and Mitsumi Profile's nut is 6mm. The nut of the profiles i use is 5mm.
I'm not sure but the widthest point for the V-slot is 9.2mm, so you can't get the right position for the MGN9 rails.

hhammarstrand, 2020-09-21:
@gsl12 Thank you for the information. I will have to find another use for the v-slot then. The plan is to build a Tiny-M when I'm done with my Switchwire.

Closed 2021-04-30.

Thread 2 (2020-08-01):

The E3D V6 print head doesn't fit, it's too tight

shenwrt, 2020-08-01:
Hello, thank you very much for your sharing, but I found that there is no model of E3D V6 in the file ".step", and the ".STL "can't be installed after it is printed directly, because it is too tight.I need your help. Could you please share the "step" file containing E3D V6? Thank you very much

shenwrt, 2020-08-01:
Google translation, please forgive me for my poor English

gsl12, 2020-08-01:
Can you try to use the onshape source files. I'm on vacation at the moment. Otherwise you will need to wait some days.

shenwrt, 2020-08-02:
Ok, I'll try. Thank you

gsl12, 2020-08-03:
I  added the cad file for E3Dv6 x-carriage.

Closed 2021-03-18.

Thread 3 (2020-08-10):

Is there a modified version of "maybe_tophat.stl"

shenwrt, 2020-08-10:
Is there a modified version of "maybe_tophat.stl",
Thank you and regards

gsl12, 2020-08-11:
No, i only print PLA or PETG with this printer, so i didn't plan to enclosure it.

BTopbas, 2020-09-07:
Enclosure and tophat mod will be great...

optizyme, 2021-04-18:
https://www.prusaprinters.org/prints/64115-tiny-m-voron0-mod-tophead
Not sure if it will work or not for you. Seems ok to me.

CroXY3D, 2021-04-30:
linked to this tophat in the readme.   Official tophat is in development and released soon.

Closed 2021-04-30.

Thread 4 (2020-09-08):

tiny-m differences?

Bluesandbox, 2020-09-08:
How different is the assembly/parts of the tiny-m mod compared to the normal voron 0, are all the parts/lengths the same, just thicker extrusions and different rails with different printed parts? and it uses mgn12 blocks and not mgn12c or mgn12h (and mgn9 and not mgn9h or mgn9c) correct?

gsl12, 2020-09-08:
The building steps are the same as for a normal V0.
Tiny-m is bigger then the normal V0. Normal V0 has a build size of 120mm³ the tiny-m has 150mm³.
For MGN please use the H blocks, like in every other Voron. C blocks are shorter then H and cannot used.

Closed 2021-03-18.

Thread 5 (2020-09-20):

Using Prusa Mini Heated Bed

BTopbas, 2020-09-20:
I want to build Tiny-M. I checked the step file and thinking to change the bed with Prusa mini bed and carriage. I need to increase the distance between bed support extrusions a little. And need some little modifications to these parts. This is meehh okay why not idea or wtf terrible idea? Here are my simulations.. (I am not professional with f360.)

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

gsl12, 2020-09-23:
I'm not sure if this will be a good or bad idea.
Problems i see:
You will lost z endstop and you will need to find another solution(position).
You will never reach each end of the bed. Prusa mini bed is 18x18cm. Tiny-M is for 15x15cm.

wesc23, 2020-11-25:
If you get this working, we can put the modified STLs in the new usermods directory here.

isulpt, 2021-01-28:
Any news about that? I have a prusa mini and interested in build a tiny-M with prusa bed.

wesc23, 2021-01-28:
There's a 180mm bed mod in the works.     Join the discord channel to see progress.

Closed 2021-04-30.

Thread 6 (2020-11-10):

Integrated leadscrew stepper?

Makhaira, 2020-11-10:
This is such a well done design, I have no need for another printer but I'm seriously considering building this. Is there a reason you have gone for a stepper and coupler onto the leadscrew, and not an integrated leadscrew stepper?

Thanks.

gsl12, 2020-11-10:
I used what I already had. Integrated leads crew should be fine too.

Closed 2021-03-18.

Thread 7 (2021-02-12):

Aluminum Bed cutting?

gitiub, 2021-02-12:
Are there any holes needed for the bed like the v0?

gsl12, 2021-02-12:
Yes three holes for the bed level screws. And maybe one for the thermal fuse, if you want to use it.

gitiub, 2021-02-12:
Is there a file for it?

gsl12, 2021-02-12:
Yes in the cad source.

Closed 2021-03-18.

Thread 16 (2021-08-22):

Can I use 2020 V-slot extrusions?

samirthegreat, 2021-08-22:

gsl12, 2021-08-22:
Because of the MGN9 the Tiny-M has the same restrictions as every other Voron. V-Slot was not recommended while the Nut is to big. MGN9 is 9mm width and Mitsumi Profile's nut is 6mm. The nut of the profiles i use is 5mm.
I'm not sure but the widthest point for the V-slot is 9.2mm, so you can't get the right position for the MGN9 rails.

danielfmo, 2021-11-02:
One option is to check a full MGN12 MOD, I thing at least one user did it, feel free to jump into the discord server

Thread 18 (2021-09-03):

190mm mod 310mm cross brace location?

dukeduck1984, 2021-09-03:
Hi,

It's mentioned in 190mm build mod that one extra 310mm extrusion is required as a cross brace to stiffen the frame.  Is there a picture to indicate where exactly that cross brace should be located?

Thanks.

danielfmo, 2021-11-02:
I'd suggest bellow the nozzle height to avoid clashes with the toolhead.
Feel free to jump into the discord server and the community will provide more help

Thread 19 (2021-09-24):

BTT mini 12864 display not working with BTT Skr mini e3 v2 board

ramsoni08, 2021-09-24:
how to connect BTT mini 12864 display with BTT Skr e3 mini v2 board ?? in klipper firmware??

properlypurple, 2021-12-01:
@ramsoni08 If you still need this to work, you should check the pinout here
https://github.com/bigtreetech/BGTHREETECH-MINI-12864-V1.0/blob/main/Hardware/BIGTREETECH%20MINI12864%20Interface.pdf

CLosing this as this is not a bug in the printer itself

jtrmal, 2021-12-01:
also this might be a solution
https://deepfriedhero.in/products/skr-mini-screen-adaptor-by-timmit99

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

Closed 2021-12-01.

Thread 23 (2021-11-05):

Why 0.9 steppers?

VICLER, 2021-11-05:
Hi @gsl12! Thanks for sharing your work!
I am actually searching and ordering parts for building my Tiny-M and I have some nema17 48mm motors with 1.8deg I wanted to use. In your BOM you recommend 0.9deg motor. Is there any print quality improvements with 0.9 instead of 1.8, or why is it recommended? Usually, 1.8deg motor has more torque than 0.9deg motor of the same size.

properlypurple, 2021-12-01:
@VICLER You can use 1.8, lots of us do. There is some discussion about this on Discord as well.

In general, 1.8 is good for speed, and 0.9 is slightly better for quality. You can get high torque 0.9 motors from LDO. I use 1.8 from a local manufacturer and they work fine.(mainly, go for what you can get easily)

VICLER, 2021-12-04:
thanks for this info!

Closed 2021-12-04.

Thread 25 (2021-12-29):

how can i use MGN9-12 with type C not H

MoustafaElkady, 2021-12-29:
Hello,
i have MGN9-12 with type C
how can i make the parts compatible?

sabaualek, 2022-09-11:
i have same issue. MGN9C on Y axis...

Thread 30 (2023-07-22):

Cooling air flow goes wrong

bi9bi9bee, 2023-07-22:
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
just as picture.

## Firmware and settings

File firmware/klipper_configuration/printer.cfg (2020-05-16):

## Tiny-M 150mm Fysetc Cheetah V1.1 TMC2209 UART config

# To use this config, the firmware should be compiled for the
# STM32F103 with "No bootloader" and with "Use USB for communication"
# disabled.

# The "make flash" command does not work on the Cheetah. Instead,
# after running "make", run the following command to flash the board:
#  stm32flash -w out/klipper.bin -v -i rts,-dtr,dtr /dev/ttyUSB0

## *** THINGS TO CHANGE/CHECK: ***
## MCU paths                      		[mcu] section
## Thermistor types                 	[extruder] and [heater_bed] sections - See 'sensor types' list at end of file
## Z Endstop Switch location       		[safe_z_home] section
## Z Endstop Switch  offset for Z0 		[stepper_z] section
## PID tune                          	[extruder] and [heater_bed] sections
## Fine tune E steps                 	[extruder] section

##========================== Pin Definitions ========================
## X_STEP_PIN         	PB8
## X_DIR_PIN          	PB9
## X_ENABLE_PIN       	PA8
## X_ENDSTOP_PIN     	PA1
## X_UART_RX          	PA3
## X_UART_TX          	PA2
## X_UART_ADDRESS		0

## Y_STEP_PIN         	PB2
## Y_DIR_PIN          	PB3
## Y_ENABLE_PIN       	PA1
## Y_ENDSTOP_PIN     	PA4
## Y_UART_RX          	PA3
## Y_UART_TX          	PA2
## Y_UART_ADDRESS		2

## Z_STEP_PIN         	PC0
## Z_DIR_PIN          	PC1
## Z_ENABLE_PIN       	PC2
## Z_ENDSTOP_PIN     	PA15
## Z_UART_RX          	PA3
## Z_UART_TX          	PA2
## Z_UART_ADDRESS		1

## E0_STEP_PIN        	PC15
## E0_DIR_PIN         	PC14
## E0_ENABLE_PIN      	PC13
## E0_UART_RX         	PA3
## E0_UART_TX         	PA2
## Z_UART_ADDRESS		3

## HE0                	PC6
## BED                	PC7
## TH0 (H0 Temp)      	PC4
## TB  (Bed Temp)     	PC5
## FAN                	PB7 # taken from RGB connectors
## FAN1              	PC8
##===================================================================

[mcu]
##	[X in X] - B Motor
##	[Y in Y] - A Motor
##	[Z in Z] - Z Motor
##	[E in E] - Extruder
##	Obtain definition by "ls -l /dev/serial/by-id/" then unplug to verify
##--------------------------------------------------------------------
serial: /dev/serial/by-id/usb-1a86_USB2.0-Serial-if00-port0
restart_method: cheetah
##--------------------------------------------------------------------

[printer]
kinematics: corexy
max_velocity: 250				#Limited for Stealthchop - Max300 for SpreadCycle
max_accel: 4000					#Max ?
#max_accel_to_decel: 3000		#default is half of max_accel
max_z_velocity: 15				#Max 30
max_z_accel: 500				#Max ?
square_corner_velocity: 5.0		#Can experiment with 8.0, default 5.0 , its like jerk

## HOMING CONFIG
[safe_z_home]
home_xy_position: 153.5,132
speed: 50.0
z_hop: 5
z_hop_speed: 10.0
move_to_previous: False

#####################################################################
# 	X/Y Stepper Settings
#####################################################################

[stepper_x]
##	Connected to X on mcu (B Motor)
step_pin: PB8
dir_pin: !PB9
enable_pin: !PA8
step_distance: .0125
endstop_pin: ^PA1
position_endstop: 153
position_min: -4
position_max: 154
homing_speed: 30			#Max 100
homing_positive_dir: true
second_homing_speed: 5
homing_retract_dist: 5

[tmc2209 stepper_x]
uart_pin: PA3
tx_pin: PA2
uart_address: 0
microsteps: 16
run_current: 0.65
hold_current: 0.6
# TMC 2209 parameters
interpolate: True
sense_resistor: 0.110
stealthchop_threshold: 0
# TMC speadcycle tuned
driver_TBL: 2
driver_TOFF: 1
# Hys = 6 == (7-3) + (1+1)
driver_HEND: 7
driver_HSTRT: 1

[stepper_y]
##	Connected to Y on mcu (A Motor)
step_pin: PB2
dir_pin: !PB3
enable_pin: !PB1
step_distance: .0125
endstop_pin: ^PB4
position_endstop: 151
position_min: -3
position_max: 151
homing_speed: 30
homing_positive_dir: true
second_homing_speed: 5
homing_retract_dist: 5

[tmc2209 stepper_y]
uart_pin: PA3
tx_pin: PA2
uart_address: 2
microsteps: 16
run_current: 0.65
hold_current: 0.60
# TMC 2209 parameters
interpolate: True
sense_resistor: 0.110
stealthchop_threshold: 0
# TMC speadcycle tuned
driver_TBL: 2
driver_TOFF: 1
# Hys = 6 == (7-3) + (1+1)
driver_HEND: 7
driver_HSTRT: 1

#####################################################################
# 	Z Stepper Settings
#####################################################################

[stepper_z]
##	Connected to Z on mcu (Z Motor)
step_pin: PC0
dir_pin: !PC1
enable_pin: !PC2
step_distance: .00125
endstop_pin: ^PA15
position_endstop: 2.1
position_min: -5
position_max: 130
homing_speed: 5
second_homing_speed: 3.0
homing_retract_dist: 3.0

[tmc2209 stepper_z]
uart_pin: PA3
tx_pin: PA2
uart_address: 1
microsteps: 32
run_current: 0.85
hold_current: 0.85
stealthchop_threshold: 100
interpolate: True

#####################################################################
# 	Extruder
#####################################################################

[extruder]
##	Connected to E on mcu (Extruder Motor)
step_pin: PC15
dir_pin: PC14
enable_pin: !PC13
heater_pin: PC6
sensor_pin: PC4
sensor_type: ATC Semitec 104GT-2
# JETPACK VORON
step_distance: 0.001801
nozzle_diameter: 0.400
filament_diameter: 1.750
# PA can be disabled by declaring a 0.0 value
##	Try to keep pressure_advance below 1.0
pressure_advance: 0.00
##	Default is 0.040, leave stock
pressure_advance_smooth_time: 0.040
instantaneous_corner_velocity: 1.0
max_extrude_only_distance: 500.0   # Bowden Length
max_extrude_only_velocity: 80
max_extrude_only_accel: 1000		# Max 3000 to much chake
max_extrude_cross_section: 20000.0 # for KISSlicer only
max_power: 1.00
smooth_time: 1
# PID V6 40WATT at 200°C
control: pid
pid_kp: 28.308
pid_ki: 1.731
pid_kd: 115.708
min_temp: 0
max_temp: 250

[tmc2209 extruder]
uart_pin: PA3
tx_pin: PA2
uart_address: 3
microsteps: 16
run_current: 0.6
hold_current: 0.6
stealthchop_threshold: 0
interpolate: True

#####################################################################
# 	Heated Bed
#####################################################################

[heater_bed]
heater_pin: PC7
sensor_type: NTC 100K MGB18-104F39050L32
sensor_pin: PC5
max_power: 0.67
min_temp: 0
max_temp: 85
control: pid
pid_kp: 45.402
pid_ki: 2.102
pid_kd: 245.173

#####################################################################
# 	Fans
#####################################################################

[fan]
pin: PB7
kick_start_time: 0.5

[heater_fan hotend_fan]
##	Hotend Fan HE1 Connector
pin: PC8
max_power: 1.0
kick_start_time: 0.5
heater: extruder
heater_temp: 50.0
##	If you are experiencing back flow, you can reduce fan_speed
fan_speed: 0.9

#####################################################################
# 	SYSTEM
#####################################################################

[idle_timeout]
gcode:
	TURN_OFF_HEATERS
	M84                            ; disable steppers
timeout: 3600

[board_pins]
aliases:
    # EXP1 header
    EXP1_1=PC9,  EXP1_3=PC11, EXP1_5=PC10, EXP1_7=PB12, EXP1_9=<GND>,
    EXP1_2=PC12, EXP1_4=PB14, EXP1_6=PB13, EXP1_8=PB15, EXP1_10=<5V>
    # Pins EXP1_4, EXP1_8, EXP1_6 are also MISO, MOSI, SCK of bus "spi2"

# See the sample-lcd.cfg file for definitions of common LCD displays.
#########################
# OPTIONAL DWC UI CONFIG
#########################
#you can also point all your printer to the same sd
[virtual_sdcard]
path: /home/pi/PrinterFarm/KlipperFarm/printer-0/sdcard

[web_dwc2]
# optional - defaulting to Klipper
printer_name: Tiny-M
# optional - defaulting to 127.0.0.1
listen_adress: 0.0.0.0
# needed - use above 1024 as nonroot
listen_port: 4750
#	optional defaulting to dwc2/web. It's a folder relative to your /home/pi/PrinterFarm/KlipperFarm/printer-0/sdcard path folder.
#web_path: /home/pi/PrinterFarm/KlipperFarm/printer-0/sdcard/dwc2/web
# optional - defaulting to /tmp/printer, needed in order to get dwc multi-session
serial_path: /tmp/printer-0
host_temp_sensor: cpu-thermal

#-----------------------------------------------------------------------------------------
#	FEATURES
#-----------------------------------------------------------------------------------------
# SET_RETRACTION [RETRACT_LENGTH=<mm>] [RETRACT_SPEED=<mm/s>] [UNRETRACT_EXTRA_LENGTH=<mm>] [UNRETRACT_SPEED=<mm/s>] [Z_HOP=<mm>]
[firmware_retraction]
retract_length: 1.6
retract_speed: 25
unretract_extra_length: 0
unretract_speed: 20

# [bed_screws] config section to enable a BED_SCREWS_ADJUST g-code
# command.
[bed_screws]
screw1: 75,5
screw1_name: front screw
screw2: 5,145
screw2_name: back left
screw3: 145,145
screw3_name: back right

#####################################################################
# 	MACROS
#####################################################################
## load from external file
[include macros.d/macros.cfg]

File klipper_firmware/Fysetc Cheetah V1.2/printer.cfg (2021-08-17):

# This file contains common pin mappings for the Fysetc Cheetah v1.2b
# board. To use this config, the firmware should be compiled for the
# STM32F103 with "No bootloader" and serial (on USART1 PA10/PA9)
# communication.

# The "make flash" command does not work on the Cheetah. Instead,
# after running "make", run the following command to flash the board:
#  stm32flash -w out/klipper.bin -v -i rts,-dtr,dtr /dev/ttyUSB0

# See docs/Config_Reference.md for a description of parameters.


[mcu]
serial: /dev/serial/by-id/usb-1a86_USB2.0-Serial-if00-port0
restart_method: cheetah

[stepper_x]
step_pin: PB8
dir_pin: !PB9
enable_pin: !PA8
microsteps: 16
full_steps_per_rotation: 400
rotation_distance: 40
endstop_pin: ^PA1
position_endstop: 153
position_max: 154
position_min: -3
homing_speed: 50

[tmc2208 stepper_x]
uart_pin: PA12
tx_pin: PA11
run_current: 1.00
hold_current: 0.500
stealthchop_threshold: 999999

[stepper_y]
step_pin: PB2
dir_pin: !PB3
enable_pin: !PB1
microsteps: 16
full_steps_per_rotation: 400
rotation_distance: 40
endstop_pin: ^PB4
position_endstop: 152.5
position_max: 152.5
position_min:-3
homing_speed: 50

[tmc2208 stepper_y]
uart_pin: PB7
tx_pin: PB6
run_current: 1.00
hold_current: 0.500
stealthchop_threshold: 999999

[stepper_z]
step_pin: PC0
dir_pin: PC1
enable_pin: !PC2
microsteps: 16
full_steps_per_rotation: 400
rotation_distance: 4
endstop_pin: ^PA15
#position_endstop: 0
position_max: 140
position_min: -3
homing_speed: 50

[tmc2208 stepper_z]
uart_pin: PB11
tx_pin: PB10
run_current: 1.00
hold_current: 0.500
stealthchop_threshold: 999999

[extruder]
step_pin: PC15
dir_pin: !PC14
enable_pin: !PC13
microsteps: 16
full_steps_per_rotation: 200 
rotation_distance: 4.077670766928368
nozzle_diameter: 0.400
filament_diameter: 1.750
heater_pin: PC6
sensor_type: EPCOS 100K B57560G104F
sensor_pin: PC4
#control: pid
#pid_kp: 21.527
#pid_ki: 1.063
#pid_kd: 108.982
min_temp: 0
max_temp: 270
max_extrude_only_distance: 780.0
max_extrude_cross_section: .8
Pressure_advance: 0.04665
pressure_advance_smooth_time: 0.040

[tmc2208 extruder]
uart_pin: PA3
tx_pin: PA2
run_current: 0.30
hold_current: 0.250
stealthchop_threshold: 999999

[heater_bed]
heater_pin: PC7
sensor_type: NTC 100K MGB18-104F39050L32
sensor_pin: PC5
#control: pid
#pid_kp: 54.027
#pid_ki: 0.770
#pid_kd: 948.182
min_temp: 0
max_temp: 130

[fan]
pin: PC8

[heater_fan nozzle_cooling_fan]
pin: PB0

[idle_timeout]
timeout: 180000

[homing_override]
axes: xyz
set_position_z: 0
gcode:
   G90
   G0 Z5 F600
   G28 X Y
   G0 X153 Y132 F3600 
   
   G28 Z
   G0 Z10 F1800
   G0 X75 Y75 Z20 F3600


[virtual_sdcard]
path: ~/uploads/

[pause_resume]

[display_status]

[gcode_macro CANCEL_PRINT]
rename_existing: BASE_CANCEL_PRINT
gcode:
    TURN_OFF_HEATERS
    CLEAR_PAUSE
    SDCARD_RESET_FILE
    BASE_CANCEL_PRINT

[gcode_macro CANCEL_PRINT]
rename_existing: BASE_CANCEL_PRINT
gcode:
    TURN_OFF_HEATERS
    CLEAR_PAUSE
    SDCARD_RESET_FILE
    BASE_CANCEL_PRINT

[gcode_macro PRINT_START]
#   Use PRINT_START for the slicer starting script - please customise for your slicer of choice
gcode:
    M140 S{BED}
    G28                            ; home all axes
    G1 Z20 F3000                   ; move nozzle away from bed
    # Wait for bed to reach temperature
    M190 S{BED}
    # Set and wait for nozzle to reach temperature
    M109 S{EXTRUDER}


   
[gcode_macro PRINT_END]
#   Use PRINT_END for the slicer ending script - please customise for your slicer of choice
gcode:

    M400                           ; wait for buffer to clear
    G92 E0                         ; zero the extruder
    G1 E-4.0 F3600                 ; retract filament
    G91                            ; relative positioning

    #   Get Boundaries
    {% set max_x = printer.configfile.config["stepper_x"]["position_max"]|float %}
    {% set max_y = printer.configfile.config["stepper_y"]["position_max"]|float %}
    {% set max_z = printer.configfile.config["stepper_z"]["position_max"]|float %}

    #   Check end position to determine safe direction to move
    {% if printer.toolhead.position.x < (max_x - 20) %}
        {% set x_safe = 20.0 %}
    {% else %}
        {% set x_safe = -20.0 %}
    {% endif %}

    {% if printer.toolhead.position.y < (max_y - 20) %}
        {% set y_safe = 20.0 %}
    {% else %}
        {% set y_safe = -20.0 %}
    {% endif %}

    {% if printer.toolhead.position.z < (max_z - 2) %}
        {% set z_safe = 2.0 %}
    {% else %}
        {% set z_safe = max_z - printer.toolhead.position.z %}
    {% endif %}

    G0 Z{z_safe} F3600    ; move nozzle up
    G0 X{x_safe} Y{y_safe} F20000    ; move nozzle to remove stringing
    TURN_OFF_HEATERS
    M107                           ; turn off fan
    G90                            ; absolute positioning
    G0 X75 Y{max_y} F3600          ; park nozzle at rear


[printer]
kinematics: corexy
max_velocity: 500
max_accel: 5000
max_z_velocity: 5
max_z_accel: 100

[board_pins]
aliases:
    # EXP1 header
    EXP1_1=PC9,  EXP1_3=PC11, EXP1_5=PC10, EXP1_7=PB12, EXP1_9=<GND>,
    EXP1_2=PC12, EXP1_4=PB14, EXP1_6=PB13, EXP1_8=PB15, EXP1_10=<5V>
    # Pins EXP1_4, EXP1_8, EXP1_6 are also MISO, MOSI, SCK of bus "spi2"

# See the sample-lcd.cfg file for definitions of common LCD displays.

#*# <---------------------- SAVE_CONFIG ---------------------->
#*# DO NOT EDIT THIS BLOCK OR BELOW. The contents are auto-generated.
#*#
#*# [extruder]
#*# control = pid
#*# pid_kp = 22.562
#*# pid_ki = 0.912
#*# pid_kd = 139.601
#*#
#*# [heater_bed]
#*# control = pid
#*# pid_kp = 58.047
#*# pid_ki = 3.172
#*# pid_kd = 265.564
#*#
#*# [stepper_z]
#*# position_endstop = -0.700
#*#
#*# [input_shaper]
#*# shaper_type_x = ei
#*# shaper_freq_x = 84.0
#*# shaper_type_y = zv
#*# shaper_freq_y = 71.8

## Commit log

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2020-05-16 Create macros.cfg
    separate macros into a file
    [macros.cfg]
2020-05-16 Update printer.cfg
    tweak some extruder settings for better retract.
    [printer.cfg]
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2020-05-20 update some parts of the project
    [x-carriage v3 - Cooling Fan Duct left V3.stl, x-carriage v3 - Cooling Fan Duct right V3.stl, x-carriage v3 - belt_retainer.stl]
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2020-06-10 klipper config updates
    klipper config modifications
    [board_pins.cfg, fans.cfg, macros.cfg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]
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2020-06-19 some changes
    removed STLs for now, made changes to klipper config
    [HyperPixel - case_middle.stl, HyperPixel - case_top.stl, ab_drive v2 - [a]_ab_drive_spacer_10mm_x2.stl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]
2020-07-07 Update Klipper config and readme
    [cancel.g, display.cfg, fans.cfg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]
2020-07-07 upload images from real printer
    [printed_parts - Spool Holder-5mm_mod.stl, printed_parts - rear_bed_mount_left.stl]
2020-07-07 upload more STL's, but still not complete.
    [printed_parts - [a]_ab_drive_spacer_10mm.stl, printed_parts - [a]_ab_drive_spacer_9mm.stl, printed_parts - a_drive_left_bottom.stl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]
2020-07-09 Backup current Klipper config
    [features.cfg, stepper.cfg, tmc2209.cfg]
2020-07-10 upload XY-joins
    There are 2 versions of the XY-Joins.
    - V2 - use GT2 20T pulleys - No Set Screw Hub
    - The outer diameter of the flanges from the pulleys for XY Joins will not fit.
    - You will need to grind the flanges to fit.
    - V3 - use GT2 20T toothed idler and no M5 Nuts
    [printed_parts - xy-join-right_top_v2.stl, printed_parts - xy-join_endstop_block.stl, printed_parts - xy-join_left_bottom_v2.stl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]
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2020-07-11 upload toolhead
    Essential part are now complete.
    [printed_parts - belt_retainer.stl, printed_parts - toolhead_fan_duct_left.stl, printed_parts - toolhead_fand_duct_right.stl]
2020-07-11 fixed CAD files
    missing parts
2020-08-03 upload CAD files for X-Carriage E3DV6
    [ass_x_carriage_E3DV6.step]
2020-09-17 Draft - BOM for the Tiny M Build
    [DRAFT - BOM - Tiny M.xlsx]
2020-09-20 Update Readme and Skirt files uploaded
    [front - front_skirt_left.stl, front - front_skirt_right.stl, side - skirt_left_back.stl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]
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2020-11-26 soon to be modded for a fan.
    [Back_Panel.DXF]
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2021-02-16 V4 files
    update to AB drive units, front-idler, xy-joint, new logo front bed mount. restructured STL folder.
    [ab_drive v4 - [a]_ab_drive_spacer_10mm.stl, ab_drive v4 - [a]_ab_drive_spacer_9mm.stl, ab_drive v4 - a_drive_left_bottom_V4.stl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]
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2021-02-17 added CAD ab drive units V4
    [ab_drive_unit_left_v4.step, ab_drive_unit_right_V4.step]
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2021-02-17 added CAD front_idler V4
    [front_idler_left_V4.step, front_idler_right_V4.step]
2021-02-17 added CAD xy-joint V4
    [xy_joint_V4.step]
2021-02-18 MGN12 X rail mod
    [Tiny-M_Extruder_for_Sherpa_Mini__MGN12H.stl, Tiny-M_Gantry_Belt_Parts.stl, Tiny-M_Umbilical_Frame.stl]
2021-02-21 added enclosure STL and CAD file V3 and V4
    [enclosure V4.step, enclosure_V3.step, enclosure_left_bottom_V3.stl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]
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2021-03-22 STL's for MGN12 V4 toolhead
    [printed_parts_MGN12_v4 - bw_dd_sch_belt_retainer.stl, printed_parts_MGN12_v4 - bw_dd_sch_belt_retainer_MGN_QC.stl, printed_parts_MGN12_v4 - bw_dd_sch_cable_pla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]
2021-03-22 Create tools - MGN12_alignment_1mm_offset.stl
    MGN12 need 1mm offset to back side.
    [tools - MGN12_alignment_1mm_offset.stl]
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2021-03-25 fixed bad step
    [ab_drive_unit_right_V4 v4.step]
2021-03-26 Create printed_parts_MGN12_v4 - bw_dd_sch_wing_sailfin.stl
    [printed_parts_MGN12_v4 - bw_dd_sch_wing_sailfin.stl]
2021-03-28 change location of klipper cheetah config
    [board_pins.cfg, display.cfg, fans.cfg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]
2021-03-28 added BTT E3 Turbo klipper config from Xile
    [printer.cfg]
2021-03-29 moved old source files to V3 folder
    [ass_x_carriage_E3DV6.step]
2021-03-31 moved old V3 toolhead STL's
    [printed_parts - belt_retainer.stl, printed_parts - toolhead_fan_duct_left.stl, printed_parts - toolhead_fand_duct_right.stl]
2021-03-31 V4 Toolhead
    move V4 toolhead files to the main folder. V4 is now the default toolhead.
    [printed_parts_MGN12_v4 - bw_dd_sch_belt_retainer.stl, printed_parts_MGN12_v4 - bw_dd_sch_belt_retainer_MGN_QC.stl, printed_parts_MGN12_v4 - bw_dd_sch_cable_pla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]
2021-04-08 Delete printed_parts_MGN12_v4 - bw_dd_sch_belt_retainer_MGN_QC.stl
    double part.
    [printed_parts_MGN12_v4 - bw_dd_sch_belt_retainer_MGN_QC.stl]
2021-04-11 back cable helper and snapshot of CAD
    [back-cable-holder-honeycomb.step, left-back-cable-holder-honeycomb.stl, right-back-cable-holder-honeycomb.stl]
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2021-04-28 Fix so shoulder secures frame vs seating on it
    [a_drive_left_top_V4.stl, ass_ab_links_V4.step, ass_ab_rechts_V4.step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]
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2021-04-30 STL's for Mini AB
    upload STL's for Mini AB for V4 Toolhead.
    [printed_parts_MGN12_v4 - bw_dd_sch_wing_mini_ab.stl, printed_parts_MGN12_v4 - mini_ab - front.stl, printed_parts_MGN12_v4 - mini_ab - front_logo.stl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]
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2021-05-02 added dragon toolhead 8mm screw modification.
    Dragon comes with M2.5x8mm screws. This version will use this screws to mount the dragon hotend.
    [toolhead_dragon_left_8mm_screw.stl, toolhead_dragon_right_8mm_screw.stl]
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2021-06-13 fix print qty
    [[a]_side_skirt_left.stl]
2021-06-13 print qty fix
    [[a]_side_skirt_left_x2.stl, skirt_side_left.stl, skirt_side_right_x2.stl]
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2021-06-29 Replaced MF105 bearings with F695 bearings in CAD
    [Bottom Frame Bracket.stl]
2021-06-29 Replaced MF105 bearings with F695 bearings in CAD, STL, and docs for belted Z mod
    [Tiny-M Belted Z BOM.xlsx]
2021-07-23 back out belt height changes
    too disruptive. GSL is doing for next rev anyway
    [[a]_a_drive_left_tensioner_V4.stl, [a]_b_drive_right_tensioner_V4.stl, a_drive_left_bottom_V4.stl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]
2021-07-23 cad revert too
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2021-08-09 Fixed rotation distance in cfg
    Had the incorrect steps for the motor, and compensated with the rotation_distance. All info has been corrected
    [printer.cfg]
2021-08-17 Organized usermods folder
    Moved around my mods to make the folder much less cluttered
    [Buck_Converter_Mount.STL, Cover_No_Logo.stl, Knob_Wrench.stl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]
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2021-10-13 Add files via upload
    Corrected mounting hole geometry and enlarged mounting holes to fit M3x5x4 heatset inserts commonly used in Voron builds.
    [SKR Mini E3 Mount with Heatset Insert.stl]
2021-10-13 Add files via upload
    Corrected mounting hole geometry.
    [RPi_Mount_v2.stl]
2021-11-25 Add a new almost all metal undercarriage mod with purge bucket
    [Brush holder tilted.3mf, bed_front_mount.3mf, bed_leadcrew_mount.3mf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]
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2021-11-26 Fix mardown
    [Brush holder tilted.3mf]
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2022-03-09 Update README.md
    fix heatset insert dims
